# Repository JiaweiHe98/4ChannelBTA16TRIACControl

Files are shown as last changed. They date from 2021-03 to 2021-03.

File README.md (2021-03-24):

# 4ChannelBTA16TRIACControl
An integrated IoT (Internet of Things) solution for controlling 4-Channel BTA16 TRIAC Board. This project is part of [ProgrammableIoTEnvironmentChamber](https://github.com/JiaweiHe98/ProgrammableIoTEnvironmentChamber).

## Overview
This section will guide you through the main progresses we have achieved.

### Web Dashboard
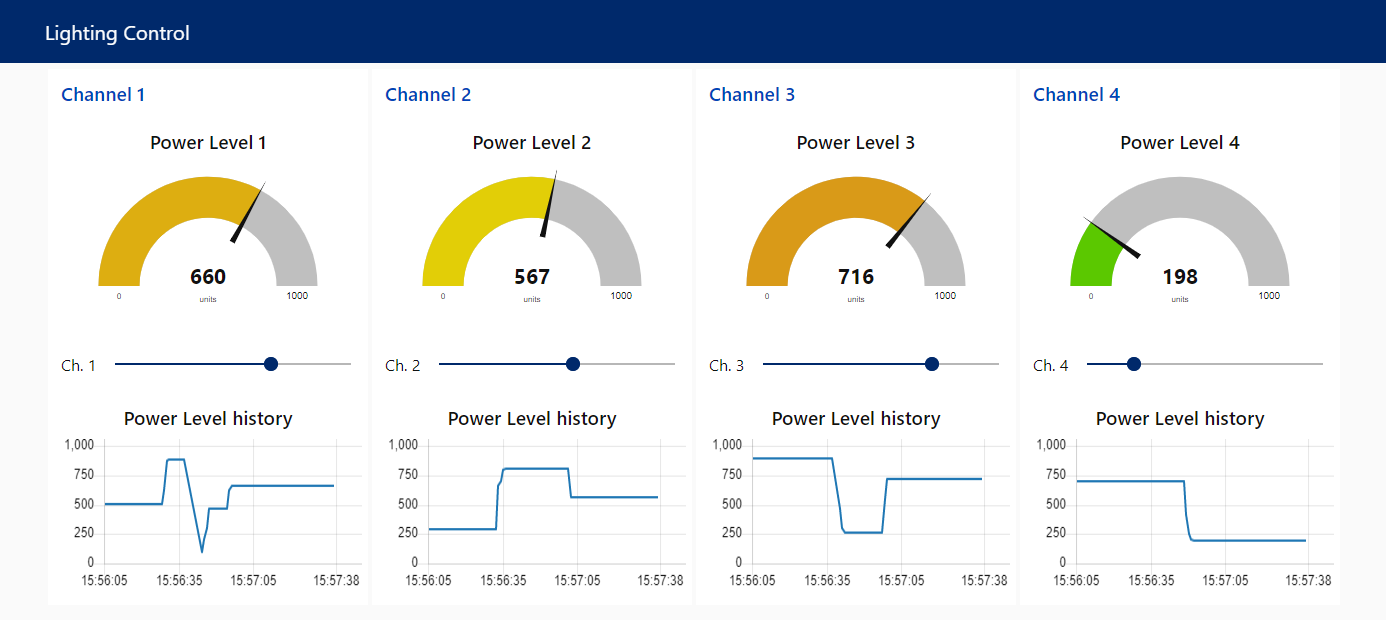
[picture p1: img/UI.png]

The gauges on the top show the current settings of each channel. The sliders below each gauge allow the users to assign new power level to each channel. We divided the power level into 1000 units. The line charts below the sliders help the users to monitor the history of the settings.

### Node-Red Flow
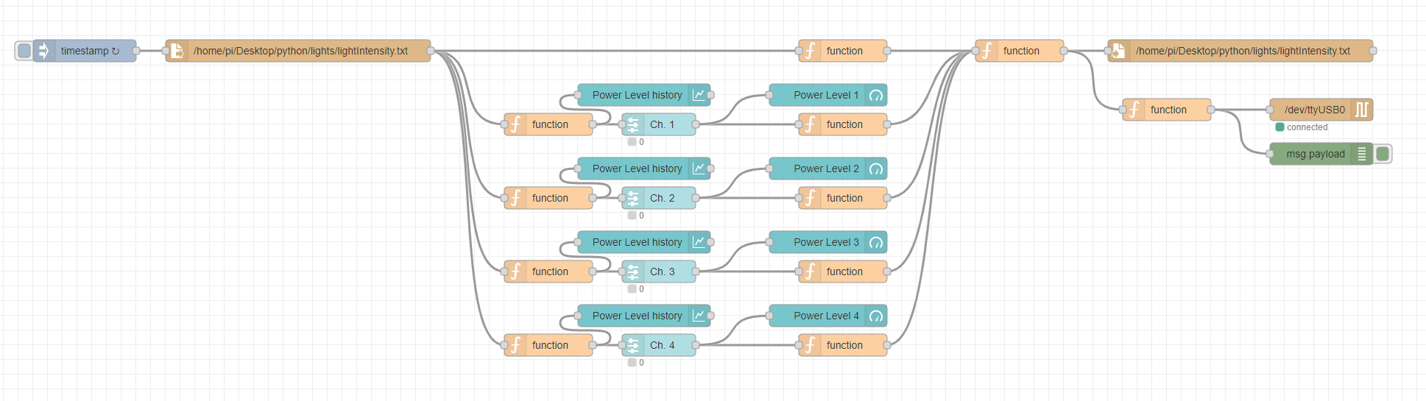
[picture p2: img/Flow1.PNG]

Node-Red is a visual programming tool based on Node.js. It allows us to use blocks and line to build our program. From the diagram above, the main steam is divided into 4 sub steams and each of them is in charge of one channel of the dimmer.

### System Diagram
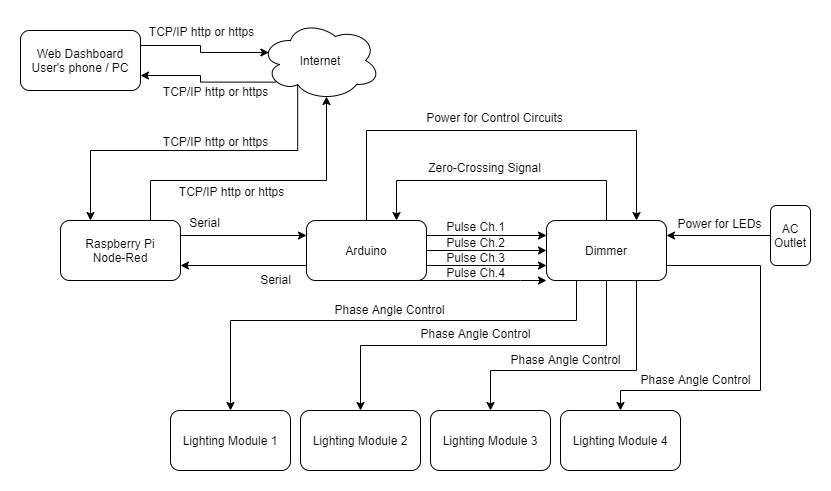
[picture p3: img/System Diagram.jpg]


### 3D Printed Control Box
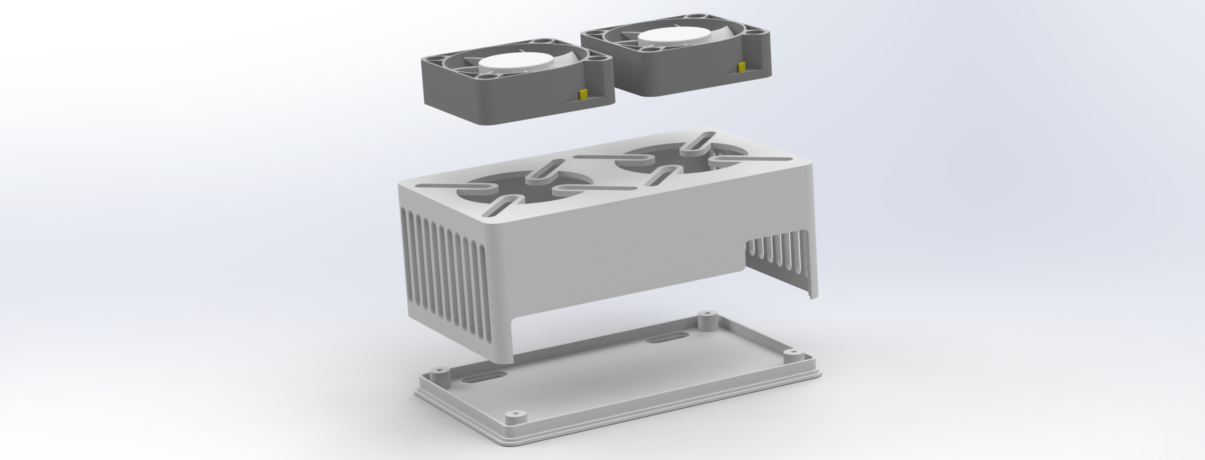
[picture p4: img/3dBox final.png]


The box can be compatible with fans range from 40mm to 70mm. It prevents electric shock caused by human contact and effectively dissipate the heat generated by the controller. For each of the base piece and the cover piece, a perfectly plain surface is designed to make the 3D printing process easier. The CAD files in both ```.SLDPRT``` and ```.STL``` can be found in the Dimmer Box CAD directory of this project.

### Dimmer
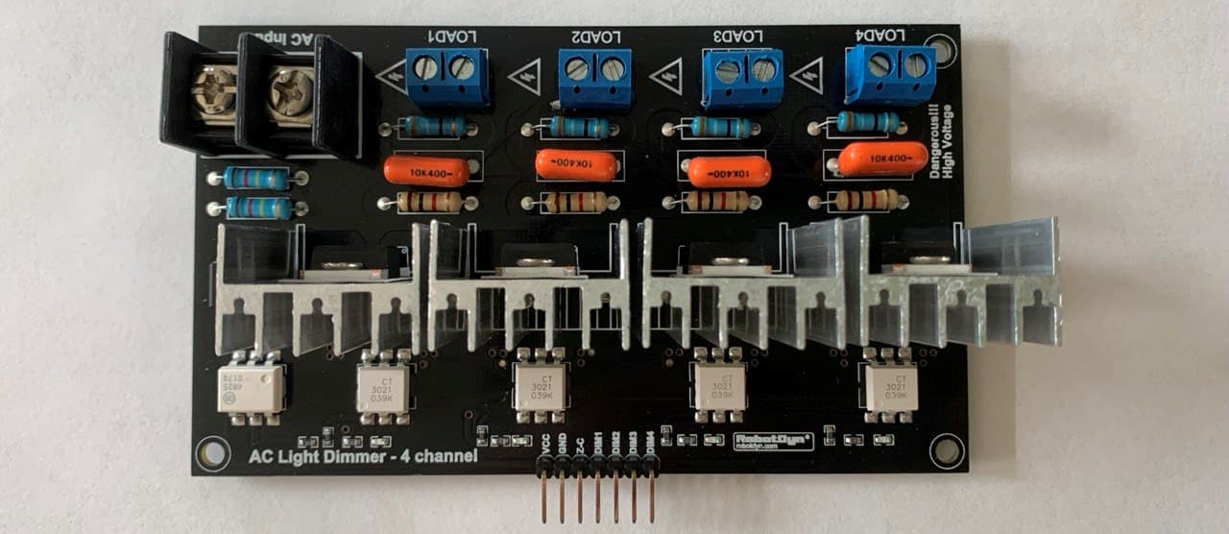
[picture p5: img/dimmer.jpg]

The control circuit is powered by outside DC sources. The main AC will only power the loads. We need to use jumper cables to connect the dimmer with the Arduino. 7 cables are required; one for VCC, one for GND, one for Zero-Crossing signal, and four for control pulse.

### Testing

Since we only have one LED at the testing time, we connected the only LED we have to each channel and do the testing separately. It works just fine. The footage above is for testing channel one.

## Prepare for Developing
This section will guide you through the software and tools required for building this project.

### Visual Studio Code
Visual Studio Code, also known as VSCode, is a popular and powerful text editor for developers. A good text editor is crucial for speeding up the coding process and debugging process.

#### Install Visual Studio Code
We recommend to use the official website for downloading the packages.
Please go to [https://code.visualstudio.com/](https://code.visualstudio.com/) and follow the instruction on the web page.

#### Recommended Extensions
We recommend you to install the listed extensions for boosting your coding experience with VSCode
* Arduino
* C/C++
* Python
* vscode-icons

### Arduino IDE
Arduino IDE is a open-source integrated development environment designated for all Arduino boards. We will use this software to compile our code and burn it to our Arduino. It also has a serial monitor which allows us to interact with Arduino through serial communication.

#### Install Arduino IDE
We also recommend to use the official website for downloading the packages if you are on a Windows or MacOS machine.
Simply go to [https://www.arduino.cc/en/software](https://www.arduino.cc/en/software) and find out your version.
If you want to use a Raspberry Pi or a Linux machine to program the Arduino, you can simply update your software list by ```sudo apt-get update``` and install Arduino IDE by ```sudo apt-get install arduino``` in your console.

### Python
Python is a widely used program language and both python2 and python3 interpreters are pre installed into Raspberry Pi OS and MacOS.

#### Install Python3 for Windows
Go to [https://www.python.org/downloads/](https://www.python.org/downloads/) and choose the version you prefer. Don't forget to add PATH for python interpreter.

#### Install pyserial package
pyserial can be installed through command line with pip. Type ```pip install pyserial``` to add pyserial library.

### Node-Red
Node-Red is a visual programming tool based on Node.js. It allows you to edit working flows inside a web browser through a wide range of nodes and deploy your flow by simply click deploy button on the right top corner.

#### Install Node-Red
If you are using Raspberry Pi and you chose "Raspberry Pi OS with desktop and recommended software", Node-red is already installed into your Raspberry Pi. Simply click the start button on the top-left and go to programming tab. Then, you will able to find Node-Red.

If you are using a Windows machine, you first need to install Node.js and nmp. Go to [https://nodejs.org/](https://nodejs.org/) and download for Windows. Run the MSI file as administrator. Accept the default settings while installing. When finishing the installation, type ```node --version; npm --version``` in Powershell or ```node --version && npm --version``` in cmd to make sure that your installation is completed.

You should see something similar to this:
```
v14.15.3
6.14.9
```

Then, install Node-Red through ```npm install -g --unsafe-perm node-red``` and add ```node-red``` to your system path.

If you are using Linux, you can install Node-Red with npm, docker, or snap. You can follow the [Documentation](https://nodered.org/docs/getting-started/local) on Node-Red official website.

#### Install node-red-dashboard
To install the node-red-dashboard, click the Menu button on the top right and select Manage palette. Then search for node-red-dashboard and click install.

Or use ```npm i node-red-dashboard``` to install it in command line.

Use [http://localhost:1880/ui](http://localhost:1880/ui) to open the dashboard if it is on you local machine. Change the URL to your server if Node-Red is running on other devices.

## Start Developing

### Phase Angle Control
Phase Angle Control is also known as "Phase-fired control (PFC)". Its principle is to modulate a thyristor or a TRIAC to control the amount of voltage, current or power flow into the controlled systems. 

#### Rectified voltage curve through Phase Angle Control
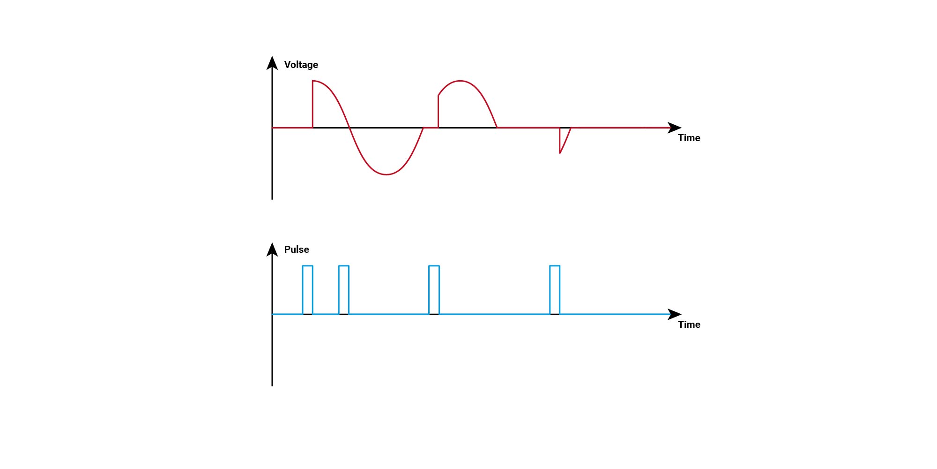
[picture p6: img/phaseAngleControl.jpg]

This project uses a BTA16 TRIAC as the device for modulate the voltage. The TRIAC will be turned on when the pulse arrive and stays on until the voltage is flipped.

### Detect Zero-Crossing points
The Zero-Crossing Points are the exact time that the AC voltage reaches zero. We first need to use a full bridge rectifier to convert AC into DC. Then we will use a optocoupler to drop the voltage from 120V or 220V to around 5V, which allows us to use an Arduino to process the signal through digital input.

#### Hardware interrupt for Arduino
The kind of interrupt we are going to use is also known as external interrupts. However, not all of the pins on the Arduino support external interrupts. For Arduino UNO, only PIN2 and PIN3 and be used as external interrupt. You can check out [attachInterrupt() - Arduino Reference](https://www.arduino.cc/reference/en/language/functions/external-interrupts/attachinterrupt/) for more information.

#### Code for external interrupt
Syntax ```attachInterrupt(digitalPinToInterrupt(pin), ISR, mode)```

| Mode | Description |
| --- | --- |
| LOW | to trigger the interrupt when the pin is low |
| CHANGE | to trigger the interrupt when the pin state flips |
| RISING | to trigger the interrupt when state goes from low to high |
| FALLING | to trigger the interrupt when state goes from high to low |
| HIGH | to trigger the interrupt when the pin is high (only support Due, Zero, and MKR1000)

Code for this project:

```C
// Define the pin number as a variable will make the developing process easier and less likely to make mistakes
int zeroCrossing = 2; 

void setup() {
  // Initialize external interrupt
  attachInterrupt(digitalPinToInterrupt(zeroCrossing), sequenceStart, FALLING);
}
```

#### Firing pulse

We choose 115200 as the baud rate and 115200 is the highest rate that Arduino support. This will allow us to have a smaller lag when we assign new instructions. We will dive deeper into the serial connect in the next section.

#### Setup:
```C
  // opens serial port, sets data rate to 115200 bps
  Serial.begin(115200);    

  // Initialize input pin
  pinMode(zeroCrossing, INPUT);

  // Initialize output pin
  pinMode(ch1, OUTPUT);
  pinMode(ch2, OUTPUT);
  pinMode(ch3, OUTPUT);
  pinMode(ch4, OUTPUT);

  digitalWrite(ch1, LOW);
  digitalWrite(ch2, LOW);
  digitalWrite(ch3, LOW);
  digitalWrite(ch4, LOW);

  // Initialize hardware interrupt, start sequence
  attachInterrupt(digitalPinToInterrupt(zeroCrossing), timerReset, FALLING);
}

```

loop: For firing the pulse (BTA16 needs around 500ns of pulse to switch it on)

```C
void loop() {

  // ch1
  if (micros() - previousMicros > timings[0] && micros() - previousMicros < timings[0] + 500)
  {
    digitalWrite(ch1, HIGH);
  } else {
    digitalWrite(ch1, LOW);
  }
  
  // ch2
  if (micros() - previousMicros > timings[1] && micros() - previousMicros < timings[1] + 500)
  {
    digitalWrite(ch2, HIGH);
  } else {
    digitalWrite(ch2, LOW);
  }

  // ch3
  if (micros() - previousMicros > timings[2] && micros() - previousMicros < timings[2] + 500)
  {
    digitalWrite(ch3, HIGH);
  } else {
    digitalWrite(ch3, LOW);
  }

  // ch4
  if (micros() - previousMicros > timings[3] && micros() - previousMicros < timings[3] + 500)
  {
    digitalWrite(ch4, HIGH);
  } else {
    digitalWrite(ch4, LOW);
  }
}

```
We cannot use delay function inside the loop because we are controlling four different channels at the same time. The delay function will tied up the CPU so that other instruction cannot be executed. Additionally, there is no operating system inside the Arduino and Arduino also does not support threading and multiprocessing. As a result, we need to store the states and make a schedule the Arduino. After that, the Arduino will become a state machine.

### Serial Communication
Serial communication allow us to send our settings to the Arduino and also let the Raspberry Pi to monitoring the working status of the Arduino.

#### Setup Serial Communication

We need to set the exact same baud rate on both the Arduino and Raspberry Pi to make it functional.

On Raspberry Pi:
```Python
import serial

# The first argument specify the serial port of the device
# Usually 'COMx' for windows, 'dev/ttyUSBx' for Raspberry Pi
arduinoData = serial.Serial('COM1', 115200)
```

On Arduino:
```C
void setup() {
  // opens serial port, sets data rate to 115200 bps
  Serial.begin(115200);  
}
```

#### Transmitting Data
From Raspberry Pi to Arduino
```Python
arduinoData.write(str(power_set).encode())
```
From Arduino to Raspberry Pi
```C
void sendPower() {
  Serial.print("[");
  for (int i = 0; i < 4; i++) {
    Serial.print(power[i]);
    if (i < 3) {
      Serial.print(",");
    }
  }
  Serial.println("]");
}
```
We only need to exchange the power levels for four channels so that we can arrange the power level into a Python list or an array. In python, we can use ```str()``` function to convert a list to a string. In arduino, we can define a small function to do the same job.

#### Receiving Data
On Raspberry Pi:
```Python
dataFromArduino = arduinoData.readline().decode('ASCII')[:-2]
power_read = eval(dataFromArduino)
```
Since we already arrange the data in the format of a Python list, we can use ```eval``` function to evaluate the string into a Python list. There will be a ```\n``` at the end of the data from Arduino. So, we can skip the last two letters.

On Arduino:
```C
void receivePower() {
  for (int i = 0; i < 4; i++) {
    power[i] = Serial.parseInt();
    timings[i] = map(power[i], 0, powerMax, 8100, 600);
  }
  bufferFlush();
  sendPower();
}
```
On Arduino we can use ```parseInt()``` function to get the settings from data sent by Raspberry Pi. ```parseInt()``` will skip the brackets and Brackets in between automatically. A serial buffer is designed to Arduino, we don't need to worry that the Arduino will miss the information sent by Raspberry Pi. We can also map the power level into the time "delay" to each zero-crossing time. We will never use a delay when multiple channels are working in the same time.

### Simplified Version
In the normal version, we added a function to the Arduino, which allows error checking by sending stored settings from Arduino back to Raspberry Pi. However, the serial communication and sending back process takes time, which will causing missing firing to the dimmer and LEDs will also blinking even frequently. Therefore, we did a simplified version which does not have the error checking function for faster response and performance.

### Direct Communication from Node-Red to Arduino
Node-Red also integrated a serial module to its programming workspace. It is also possible to use control the Arduino without the Python script. We have already tested connecting Raspberry Pi to Arduino without Python script and the whole system work just fine. So, if you are not familiar with Python, we recommend you to do it directly.

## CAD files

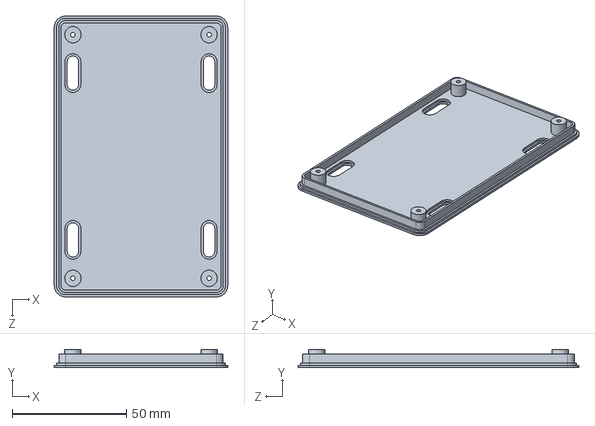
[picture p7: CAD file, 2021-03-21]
Dimmer Box CAD/base.SLDPRT
76.0 x 8.00 x 123.0 mm

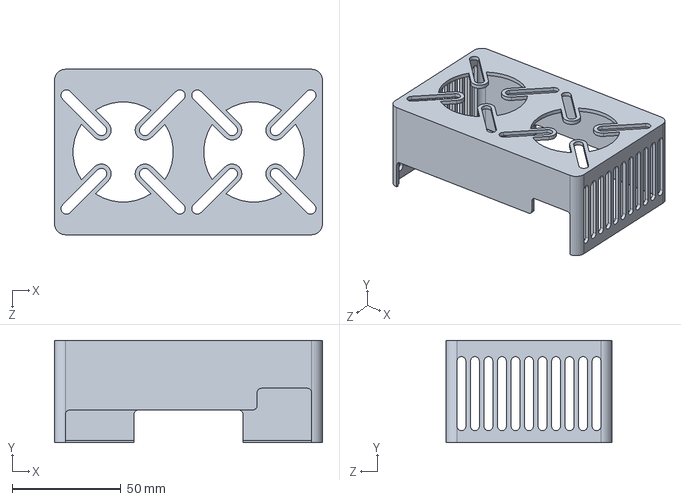
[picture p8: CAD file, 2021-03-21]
Dimmer Box CAD/cover.SLDPRT
123.0 x 47.0 x 76.0 mm

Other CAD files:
Dimmer Box CAD/base.STL
Dimmer Box CAD/cover.STL

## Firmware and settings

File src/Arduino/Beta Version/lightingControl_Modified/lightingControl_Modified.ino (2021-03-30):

// Store the time of last zero-crossing
unsigned long previousMicros = micros();

//Store the time of last time sending back settings
unsigned long sendBack = micros();

// Channel number to pin number
int ch1 = 8;
int ch2 = 9;
int ch3 = 10;
int ch4 = 11;

// Zero-crossing point detection
int zeroCrossing = 2;

// Power output initialization
int power[4] = {1, 1, 1, 1};
int powerMax = 100;

// Firing "delay"
int timings[4] = {8100, 8100, 8100, 8100};

// Setup serial connection and define pins
void setup() {
  // opens serial port, sets data rate to 115200 bps
  Serial.begin(115200);    

  // Initialize input pin
  pinMode(zeroCrossing, INPUT);

  // Initialize output pin
  pinMode(ch1, OUTPUT);
  pinMode(ch2, OUTPUT);
  pinMode(ch3, OUTPUT);
  pinMode(ch4, OUTPUT);

  digitalWrite(ch1, LOW);
  digitalWrite(ch2, LOW);
  digitalWrite(ch3, LOW);
  digitalWrite(ch4, LOW);

  // Initialize hardware interrupt, start sequence
  attachInterrupt(digitalPinToInterrupt(zeroCrossing), timerReset, FALLING);

}

//Call functions in order
void loop() {

  // ch1
  if (micros() - previousMicros > timings[0] && micros() - previousMicros < timings[0] + 500)
  {
    digitalWrite(ch1, HIGH);
  } else {
    digitalWrite(ch1, LOW);
  }
  
  // ch2
  if (micros() - previousMicros > timings[1] && micros() - previousMicros < timings[1] + 500)
  {
    digitalWrite(ch2, HIGH);
  } else {
    digitalWrite(ch2, LOW);
  }

  // ch3
  if (micros() - previousMicros > timings[2] && micros() - previousMicros < timings[2] + 500)
  {
    digitalWrite(ch3, HIGH);
  } else {
    digitalWrite(ch3, LOW);
  }

  // ch4
  if (micros() - previousMicros > timings[3] && micros() - previousMicros < timings[3] + 500)
  {
    digitalWrite(ch4, HIGH);
  } else {
    digitalWrite(ch4, LOW);
  }

  //Receive settings
  if (Serial.available() > 0) {
    int temp;
    for (int i = 0; i < 4; i++) {
      temp = Serial.parseInt();
      if (temp > 0 && temp < 101) {
        power[i] = temp;
        timings[i] = map(power[i], 0, powerMax, 8100, 800);
      } else {
        break;
      }
    }
    bufferFlush();
  }

}

void timerReset() {
  previousMicros = micros();
}

//Flush the remaining garbage information in serial buffer
void bufferFlush() {
  while(Serial.available() > 0) {
    char t = Serial.read();
  }
}

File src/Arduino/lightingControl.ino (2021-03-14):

//Main Timer
unsigned long startTime = micros();

// Channel number to pin number
int ch1 = 8;
int ch2 = 9;
int ch3 = 10;
int ch4 = 11;

// Zero-crossing point detection
int zeroCrossing = 2;

// Power output initialization
int power[4] = {0, 0, 0, 0};
int powerMax = 1000;

//Flag
bool isChanged = false;

// Firing queue initialization. 8333 to 0
int timings[8] = {-1, -1, -1, -1, -1, -1, -1, -1};
int channelNum[8] = {ch1, ch1, ch2, ch2, ch3, ch3, ch4, ch4};
bool states[8] = {true, false, true, false, true, false, true, false};

//sand back
unsigned long sendBack = millis();

// Setup serial connection and define pins
void setup() {
    // opens serial port, sets data rate to 115200 bps
    Serial.begin(115200);    

    // Initialize input pin
    pinMode(zeroCrossing, INPUT);

    // Initialize output pin
    pinMode(ch1, OUTPUT);
    pinMode(ch2, OUTPUT);
    pinMode(ch3, OUTPUT);
    pinMode(ch4, OUTPUT);

    // Initialize hardware interrupt, start sequence
    attachInterrupt(digitalPinToInterrupt(zeroCrossing), sequenceStart, FALLING);

    // send initial power level
    sendPower();
}

//Call functions in order
void loop() {

  //Save power
  if (micros() - startTime > 10^7) {
    delay(1000);
  }
  
  //Receive settings
  if (Serial.available() > 0) {
    receivePower();
  }

  //Update settings
  if (isChanged) {
    makeQueue();
    isChanged = false;
  }

  //Send back power levels
  if ((millis() - sendBack) > 10000) {
    sendPower();
    sendBack = millis();
  }

  // for debugging
//  delay(1000);
//  sendPower();
//  sequenceStart();
}


//For receiving settings
void receivePower() {
  for (int i = 0; i < 4; i++) {
    power[i] = Serial.parseInt();
  }
  bufferFlush();
  isChanged = true;
  sendPower();
}

//Send back power levels
void sendPower() {
  Serial.print("[");
  for (int i = 0; i < 4; i++) {
    Serial.print(power[i]);
    if (i < 3) {
      Serial.print(",");
    }
  }
  Serial.println("]");

// For debuging
//  Serial.print("[");
//  for (int i = 0; i < 8; i++) {
//    Serial.print(timings[i]);
//    if (i < 7) {
//      Serial.print(",");
//    }
//  }
//  Serial.println("]");
//  
//  Serial.print("[");
//  for (int i = 0; i < 8; i++) {
//    Serial.print(channelNum[i]);
//    if (i < 7) {
//      Serial.print(",");
//    }
//  }
//  Serial.println("]");
//
//  Serial.print("[");
//  for (int i = 0; i < 8; i++) {
//    Serial.print(states[i]);
//    if (i < 7) {
//      Serial.print(",");
//    }
//  }
//  Serial.println("]");
}

//Flush the remaining garbage information in serial buffer
void bufferFlush() {
  while(Serial.available() > 0) {
    char t = Serial.read();
  }
}

//Sending pulse to the dimmer
void firing(int chNum, bool state) {
  if (state) {
    digitalWrite(chNum, HIGH);
  } else {
    digitalWrite(chNum, LOW);
  }
}

//Make a queue for pulling up and pulling down the voltage of control pins
void makeQueue() {

  //Temporary arrays 
  int timeOn[4];
  int timeOnPin[4] = {ch1, ch2, ch3, ch4};
  int timeOff[4];
  int timeOffPin[4] = {ch1, ch2, ch3, ch4};

  //Push settings into temporary arrays. If power level is 0, output -1 for skipping the pulse
  for (int i = 0; i < 4; i++) {
    if (power[i] == 0) {
      timeOn[i] = -1;
      timeOff[i] = -1;
    } else {
      timeOn[i] = map(power[i], 0, powerMax, 8333, 0);
      timeOff[i] = timeOn[i] + 500;
    }
  }

  //Temporary variables for sorting
  int index;
  int minNum;
  int temp;

  //Sort timings of pulling up
  for (int i = 0; i < 3; i++) {
    minNum = timeOn[i];
    index = i;
    for (int j = i + 1; j < 4; j++) {
      if (timeOn[j] < minNum) {
        minNum = timeOn[j];
        index = j;
      }
    }
    if (index != i) {
      temp = timeOn[i];
      timeOn[i] = timeOn[index];
      timeOn[index] = temp;

      temp = timeOnPin[i];
      timeOnPin[i] = timeOnPin[index];
      timeOnPin[index] = temp;
    }
  }

  //sort timings of pulling down
  for (int i = 0; i < 3; i++) {
    minNum = timeOff[i];
    index = i;
    for (int j = i + 1; j < 4; j++) {
      if (timeOff[j] < minNum) {
        minNum = timeOff[j];
        index = j;
      }
    }
    if (index != i) {
      temp = timeOff[i];
      timeOff[i] = timeOff[index];
      timeOff[index] = temp;

      temp = timeOffPin[i];
      timeOffPin[i] = timeOffPin[index];
      timeOffPin[index] = temp;
    }
  }

  //merge 4 array
  int onIndex = 0;
  int offIndex = 0;
  int queueIndex = 0;

  while (onIndex < 4 && offIndex < 4) {
    if (timeOn[onIndex] < timeOff[offIndex]) {
      timings[queueIndex] = timeOn[onIndex];
      channelNum[queueIndex] = timeOnPin[onIndex];
      states[queueIndex] = true;
      onIndex ++;
    } else {
      timings[queueIndex] = timeOff[offIndex];
      channelNum[queueIndex] = timeOffPin[offIndex];
      states[queueIndex] = false;
      offIndex ++;
    }
    queueIndex ++;
  }

  if (onIndex >= 4) {
    while (queueIndex < 8) {
      timings[queueIndex] = timeOff[offIndex];
      channelNum[queueIndex] = timeOffPin[offIndex];
      states[queueIndex] = false;
      offIndex ++;
      queueIndex ++;
    }
  } else {
    while (queueIndex < 8) {
      timings[queueIndex] = timeOn[onIndex];
      channelNum[queueIndex] = timeOnPin[onIndex];
      states[queueIndex] = true;
      onIndex ++;
      queueIndex ++;
    }
  }
  
}

//Set zero crossing time
void sequenceStart() {

  //get start time
  startTime = micros();

  //initialize current time
  unsigned long timeNow;

  //start sequence
  for (int i = 0; i < 8; i ++) {
    timeNow = micros();
    if ((timeNow - startTime) < timings[i]) {
      delayMicroseconds(timings[i] - (timeNow - startTime));
    }

    //skip 0 power level
    if (timings[i] != -1) {
      firing(channelNum[i], states[i]);

      // for debugging
//      Serial.print("channelNum:");
//      Serial.print(channelNum[i]);
//      Serial.print("states:");
//      Serial.print(states[i]);
//      Serial.print("time:");
//      Serial.println(micros() - startTime);
    }
  }
}

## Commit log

2021-03-19 Added threading to backend script
2021-03-21 Added CAD model, updated Node-Red flow, modified the document, and recorded a small testing video
    [base.SLDPRT, base.STL, cover.SLDPRT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]
2021-03-24 Fixed Ch.1 in Arduino Code and md
    [lightingControl_v1.ino]
2021-03-30 Added 1 to 100 power level version
